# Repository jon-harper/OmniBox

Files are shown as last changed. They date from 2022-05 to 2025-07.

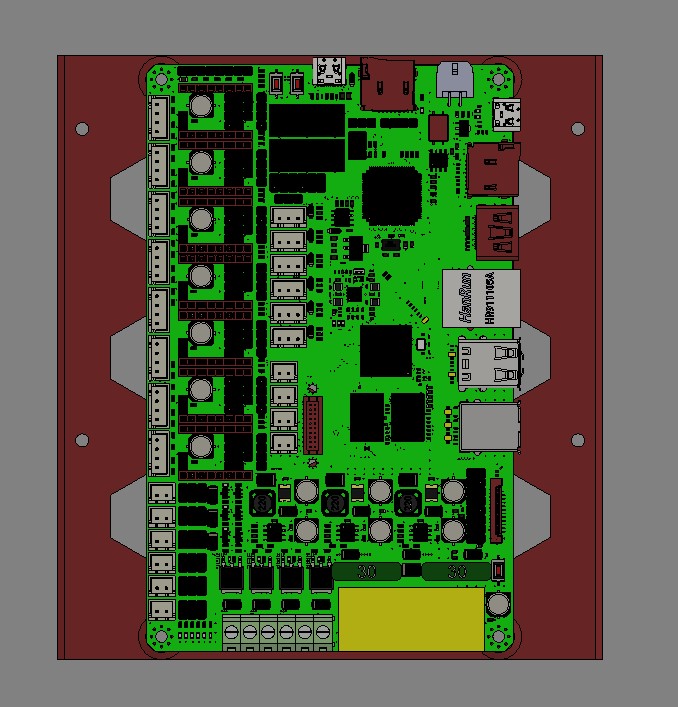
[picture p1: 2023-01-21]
Trays/MCU/MKS Skipr/Contrib/Screenshot 2022-11-25 044527.jpg

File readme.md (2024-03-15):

Welcome to the OmniBox repository! OmniBox is a modular, 3D printed electronics case for controlling 3D printers. It is conceptually derived from Steve Burcham's **[Stand Alone Main Control Case](https://github.com/bgdog1/3dPrinterCase)** V3.

This project focuses on modularity, accessibility to users, and reusability. The goal of OmniBox is to make your printer's electronics as valuable and re-usable an asset as the printer it controls.

## Documentation & Help

The **[Documentation][latest_docs]** includes a visual tour, a full bill of materials, list of supported parts, and guides for both printing and assembly.

Drop by the **[OmniBox Discord server](https://discord.gg/nKmJZMhfz5)** if you have other questions, or if you are simply curious!

## Current Release

v0.9.11 is the most recent stable version, released 2024/03/15.

- **[v0.9.11 Documentation][latest_docs]**
- **[v0.9.11 Changelog][changelog]**

photobooth picture

[changelog]: https://jon-harper.github.io/OmniBox/latest/history/
[latest_docs]: https://jon-harper.github.io/OmniBox/latest
[testing_changelog]: https://jon-harper.github.io/OmniBox/testing/history/
[testing_docs]: https://jon-harper.github.io/OmniBox/testing
[gallery_pic]:  https://jon-harper.github.io/OmniBox/0.9.11/img/examples/0.9.11/banner.png
[unstable]: https://github.com/jon-harper/OmniBox/tree/unstable

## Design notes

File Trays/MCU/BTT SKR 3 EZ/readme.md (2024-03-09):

# Trays/MCU/BTT SKR

## Overview

This tray mounts a BIGTREETECH SKR 3 EZ board. It is *not* compatible with the regular SKR 3.

- Category: MCU Tray
- Product: BIGTREETECH SKR 3 EZ
- Added: 0.9.9

## STL Files

### `MCU Tray - BTT SKR 3 EZ - M3.stl`

- Supports: No
- Mounting Hardware: 4x M3 x 6mm machine screws

### `MCU Tray - BTT SKR 3 EZ - M4.stl`

Note: M4 files are for users of 0.9.8 and earlier and are deprecated.

- Supports: No
- Mounting Hardware: 4x M4 x 6mm machine screws

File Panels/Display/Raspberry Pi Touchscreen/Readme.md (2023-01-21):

# Display Panel for Raspberry 7" Touchscreen

This plate mounts official Raspberry [Pi Touch Display](https://www.raspberrypi.com/products/raspberry-pi-touch-display/) to the OmniBox.

As the display is quite big, it covers the screw holes on the front body, so I recommend
installing the display first on the front part, before attaching it to the base.

Connect all the wires to the display first, both SPI and power, before mounting it to the plate.

There are two versions available, one is flush with the main body face and one is slightly raised.
The only differences are in the aesthetics and the screw size required.

- Flush version requires four M3x8 screws to mount the display. Both parts are attached to the main body first.
- Raised version requires four M3x16 screws to mount the display. You need to attach the plate first to the main body and then attach the display with the case to it.

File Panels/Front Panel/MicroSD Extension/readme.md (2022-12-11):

## Don't forget the SD Card extension files!

Make sure you also print the holder and cap files in `Misc/Micro SD Extension`.

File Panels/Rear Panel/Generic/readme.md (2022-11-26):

# Generic Panels

Each subfolder contains panels have cutouts to run wires through instead of panel mounts. Most users will want to use one of these.

There are still two configuration options:

## USB Port

- No USB panel mount
- USB B panel mount (SKR and most other boards)
- USB C panel mount (BTT Octopus and many newer boards)

Micro-USB to USB B panel mount connectors are available. Ex: Old Creality and many 8-bit boards use Micro-USB.

## 60mm Fan Cutout

Each panel has a version with this cutout if you want to use a 60mm fan instead of (or in addition to) the default dual 40mm fans.

These panels are all made from the same template. The source Fusion file also includes an 80mm fan profile if you'd like to go larger.

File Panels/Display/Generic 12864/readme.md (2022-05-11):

## Attribution

The contents of this folder are part of Steve Burcham's [3DPrinterCase](https://www.thingiverse.com/thing:3999751) project and are his designs. They have been slightly modified to remove some mounting holes.

## License

These files are individually licensed under the [Creative Commons - Attribution](https://creativecommons.org/licenses/by/4.0/) license.

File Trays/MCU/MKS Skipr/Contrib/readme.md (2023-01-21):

# MKS Skipr 1.0

This is a contributed tray for the MKS Skipr that uses 4mm long M3 inserts. These are more commonly found than the longer inserts used for the Core body.

## Credits

[Killajoedotcom](https://github.com/Killajoedotcom)

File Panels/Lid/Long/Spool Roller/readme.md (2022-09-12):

# Spool Roller Lid

The STL files in this folder are for a lid that doubles as a platform/mount for a spool roller.

This lid is based on my [Tighter T.U.S.H.](https://www.thingiverse.com/thing:4737072) filament roller project on Thingiverse.

This component was introduced in version 0.9.8.1.

## Bill of Materials

| Item | Qty |
|---|-----|
| `Lid - Spool Roller.stl` | 1 ea |
| `Spool Roller.stl` | 4 ea |
| M3 x 16mm machine screws | 4 ea |
| 608ZZ ball bearings | 4 ea |

## Instructions

1. Print one (1) of the lid file and four (4) of the spool roller files.
2. Set a spool roller flat in front of you.
3. There are two standoffs in on each side of the spool roller, both with holes in them. Set a 608ZZ ball bearing on each one.
4. The standoffs should go halfway up the center of the ball bearings. Take another spool holder and place it face down so that the standoffs meet in the ball bearing.
5. Insert an M3 screw in the left hole (the larger one) and screw it tight.
6. Flip the assembly over and insert an M3 screw in the left (larger) hole and tighten.
7. Repeat steps 2-6 to make another spool roller.
8. Snap the rollers onto the lid guide and adjust the distance between the rollers for brand of filament.

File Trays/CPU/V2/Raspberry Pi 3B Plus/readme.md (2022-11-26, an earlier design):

# Trays/CPU/Raspberry Pi 3B Plus

## Overview

This tray mounts a single Raspberry Pi 3B+.

- Category: CPU Tray
- Product: Raspberry Pi 3B+
- Added: 0.9
- Updated: 0.9.9

## STL Files

### `CPU Tray - RPi 3B Plus.stl`

- Supports: Recommended
- Mounting Hardware: 4x M3 x 6mm machine screws

### `CPU Tray - RPi 3B Plus with SPI.stl`

- Supports: Recommended
- Mounting Hardware: 4x M3 x 6mm machine screws
- Additional Hardware: 
	- 1x Micro Fit 3 panel mount connector, 2 Row, 6 Position (for SPI port)

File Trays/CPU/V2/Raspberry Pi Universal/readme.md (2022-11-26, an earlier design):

# Trays/CPU/Raspberry Pi 4B

## Overview

This tray mounts a single Raspberry Pi 3B+ or 4B. It is also compatible with clones that mount using the Raspberry Pi mounting hole pattern.

- Category: CPU Tray
- Product: Raspberry Pi SoC Form Factor
- Added: 0.9.9

## STL Files

### `CPU Tray - RPi with Fan.stl`

- Supports: Optional/use support blockers
- Mounting Hardware: 4x M3 x 6mm machine screws
- Additional hardware:
    - 1x 40mm fan
    - 4x M3 x 16 screws
	
### `CPU Tray - RPi with Fan and SPI.stl`

- Supports: Optional/use support blockers
- Mounting Hardware: 4x M3 x 6mm machine screws
- Additional hardware:
    - 1x 40mm fan
    - 4x M3 x 16 screws
	- 1x Micro Fit 3 panel mount connector, 2 Row, 6 Position (for SPI port)

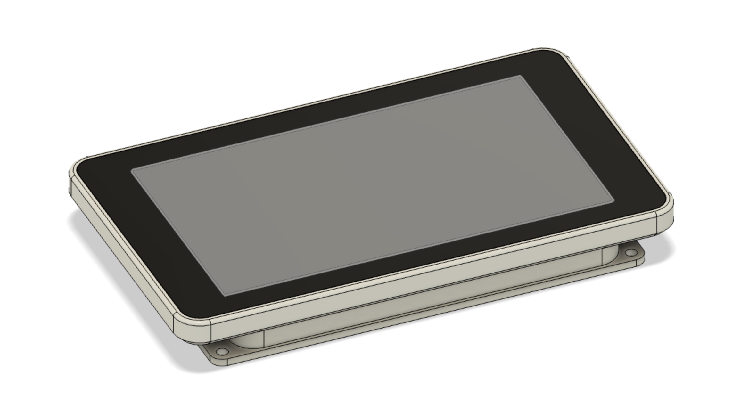
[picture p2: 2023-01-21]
Panels/Display/Raspberry Pi Touchscreen/raised/view_top.png

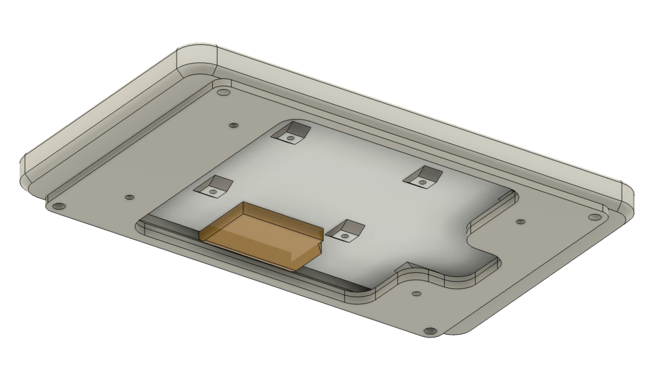
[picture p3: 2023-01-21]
Panels/Display/Raspberry Pi Touchscreen/flat/view_bottom.png

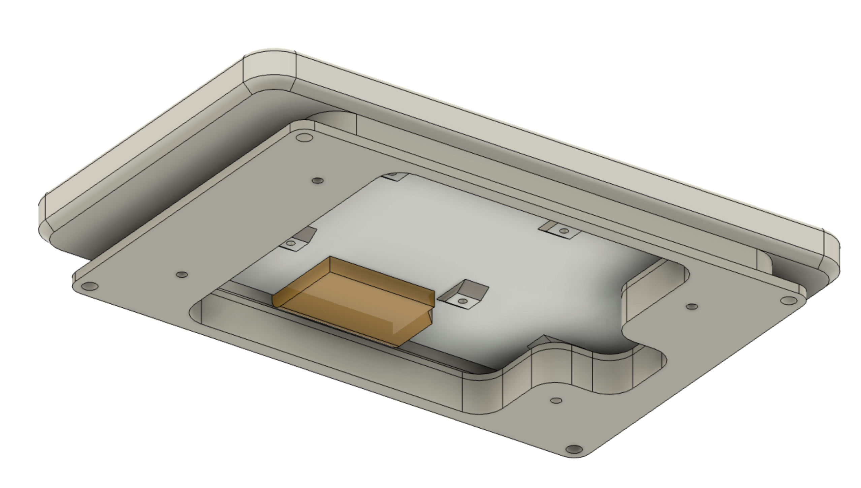
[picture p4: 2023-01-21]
Panels/Display/Raspberry Pi Touchscreen/raised/view_bottom.png

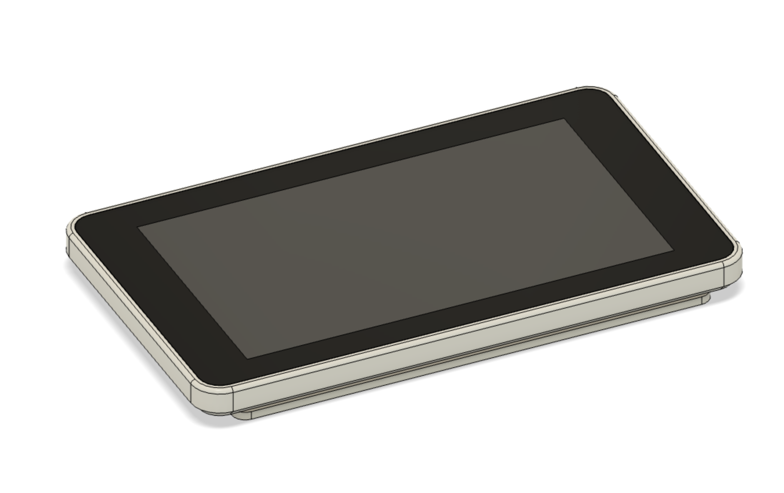
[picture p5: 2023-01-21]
Panels/Display/Raspberry Pi Touchscreen/flat/view_top.png

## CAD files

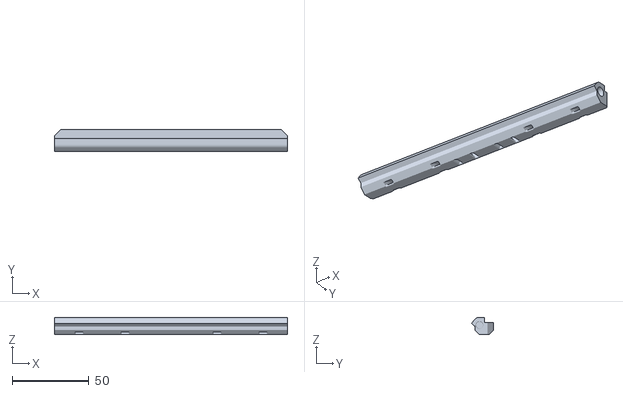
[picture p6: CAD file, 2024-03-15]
Core/Main Body/Crossbar/Main Body - Crossbar - HSI.stl
152.0 x 14.5 x 11.2

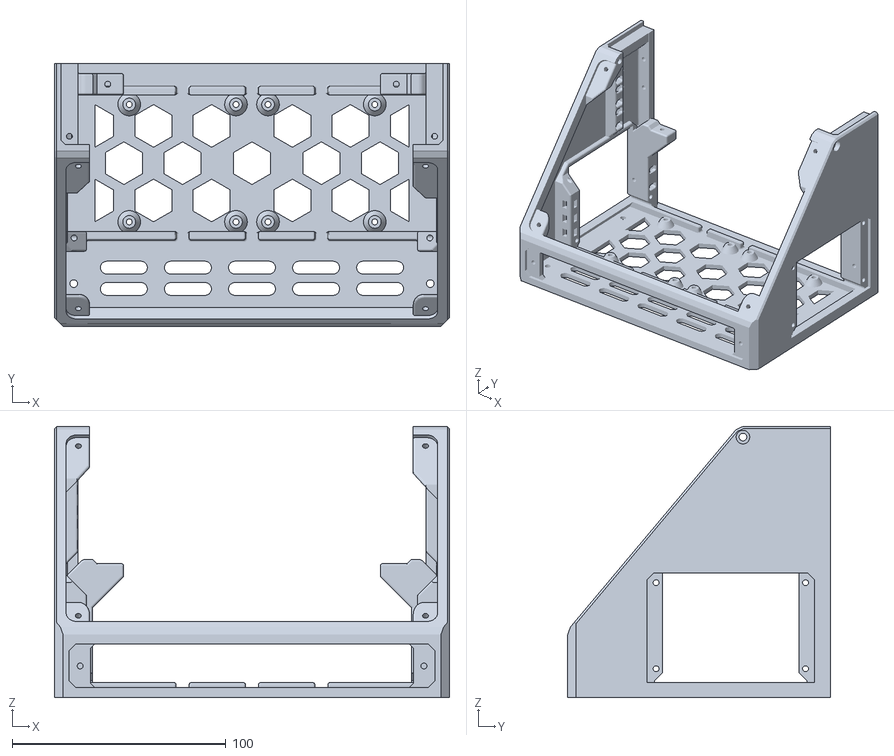
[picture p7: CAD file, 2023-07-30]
Core/Main Body/Front/Main Body - Front - Stock.stl
185.0 x 123.0 x 127.0

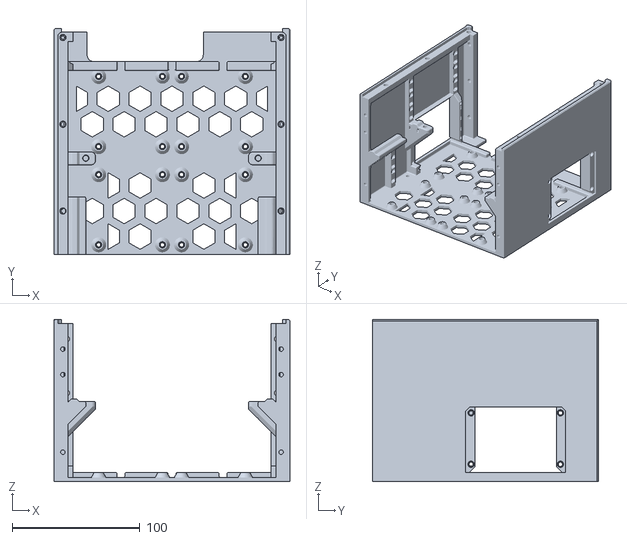
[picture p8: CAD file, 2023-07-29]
Core/Main Body/Rear/Main Body - Rear - Full HSI.stl
185.0 x 177.0 x 127.0

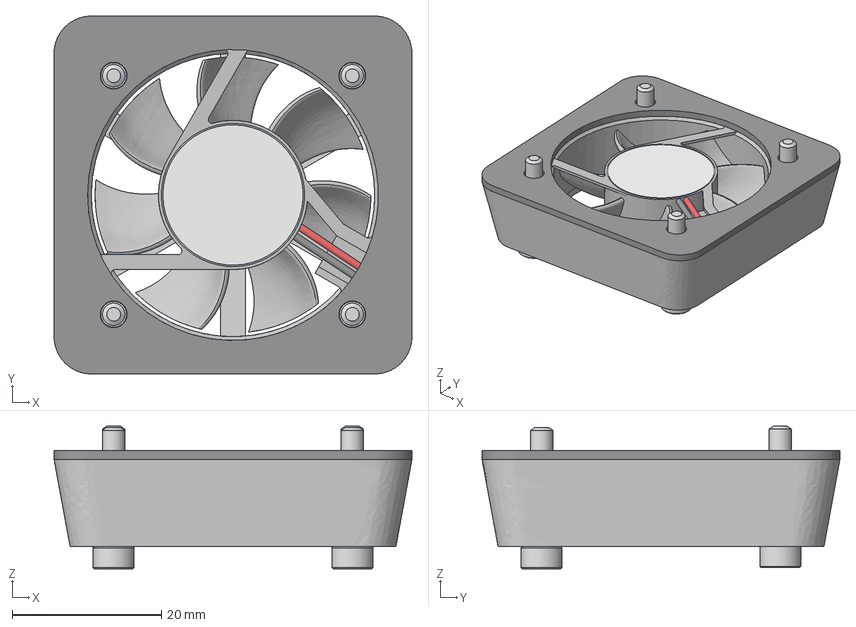
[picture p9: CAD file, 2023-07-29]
Fans/40x10/4010 Fan Assembly.step
48.0 x 48.0 x 19.2 mm
4010 Fan Cage
4010 Fan Gasket
PN503 x 4
PN700

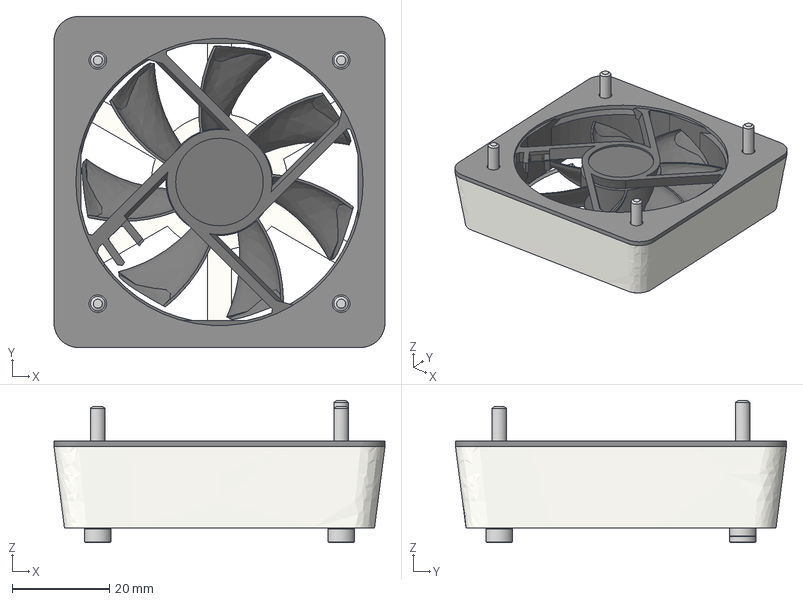
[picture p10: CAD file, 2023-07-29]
Fans/60x15/6015 Fan Assembly.step
68.0 x 68.0 x 29.2 mm
6015 Fan Cage
6015 Fan Gasket
PN505 x 4
Fan Wheel
Fan-Sunont_60x60x15mm

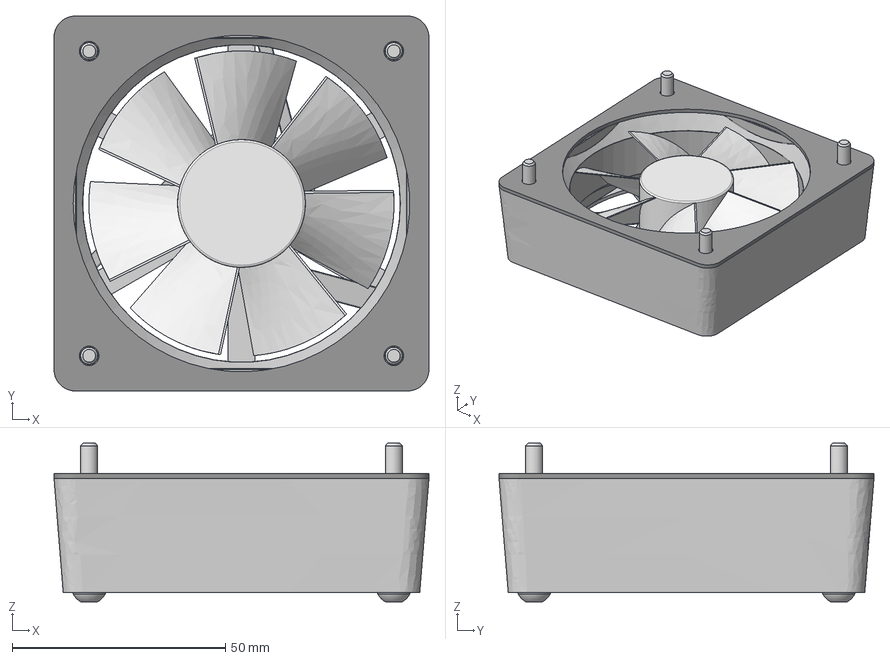
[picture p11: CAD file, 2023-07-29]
Fans/80x25/8025 Fan Assembly.step
88.0 x 88.0 x 37.2 mm
8025 Fan Cage
8025 TPU Gasket
80MM_FAN_PROP
80MM_FAN_HOUSING
PN517 x 4

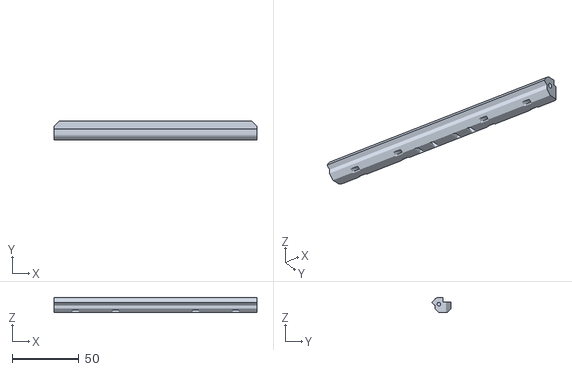
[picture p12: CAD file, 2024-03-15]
Core/Main Body/Crossbar/Main Body - Crossbar - Stock.stl
152.0 x 14.5 x 11.2

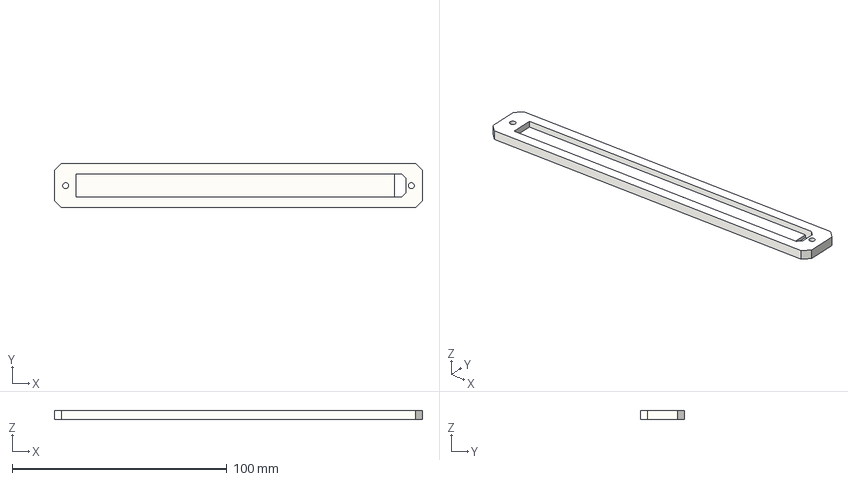
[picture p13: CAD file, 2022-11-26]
Misc/Front Panel LED Backer/Front Panel LED Backer - Full Length.step
171.4 x 20.4 x 4.20 mm

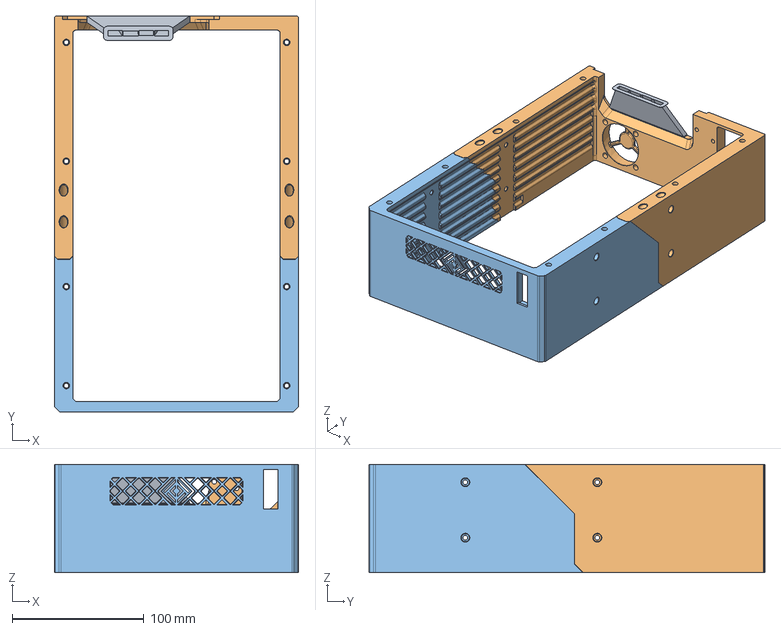
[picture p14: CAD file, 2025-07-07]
CAD/Double Base V4 - HSI.step
185.0 x 300.0 x 82.0 mm
Base Supports v4
Base - 70mm Front - HSI

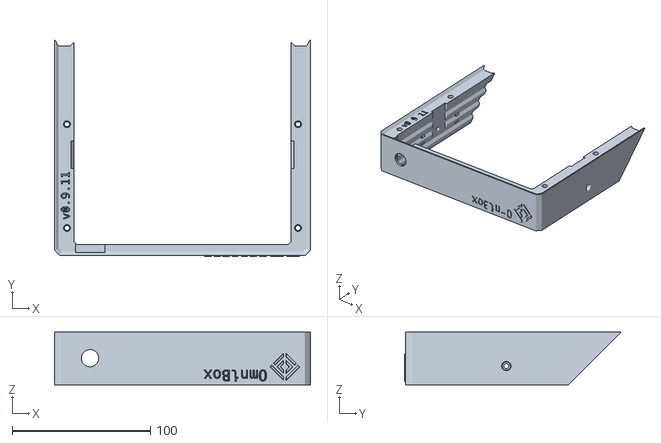
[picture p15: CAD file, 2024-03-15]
Core/Base/36mm HSI/Front/Base - 36mm Front - HSI with Toggle.stl
185.0 x 156.5 x 38.0

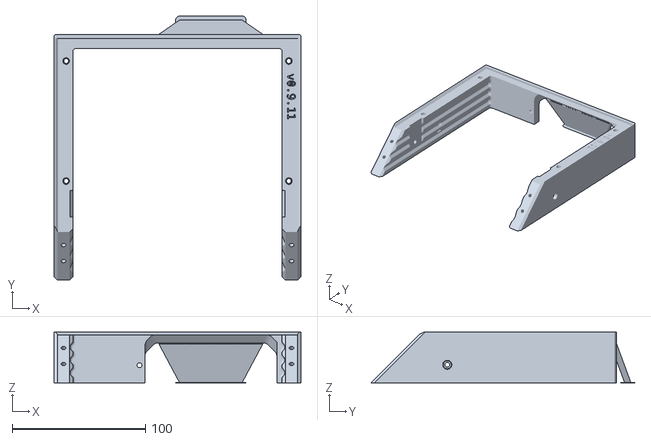
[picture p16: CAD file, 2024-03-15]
Core/Base/36mm HSI/Rear/Base - 36mm Rear - Basic HSI.stl
185.0 x 197.9 x 38.0

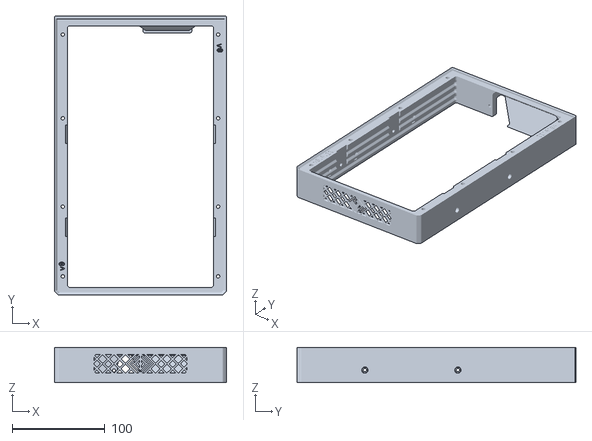
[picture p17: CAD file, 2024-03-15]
Core/Base/36mm HSI/Unified/Base - 36mm Unified - Basic HSI.stl
185.0 x 300.0 x 38.0

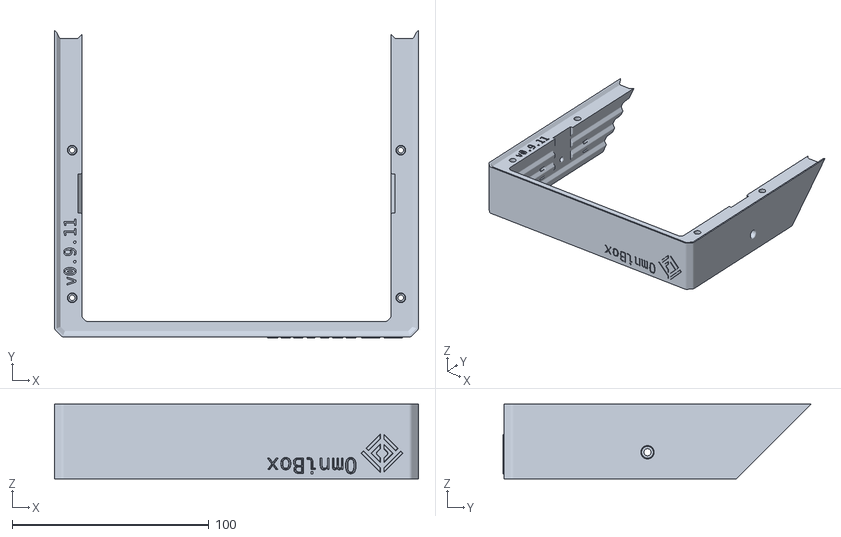
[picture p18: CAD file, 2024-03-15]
Core/Base/36mm Stock/Front/Base - 36mm Front - Basic Stock.stl
185.0 x 156.5 x 38.0

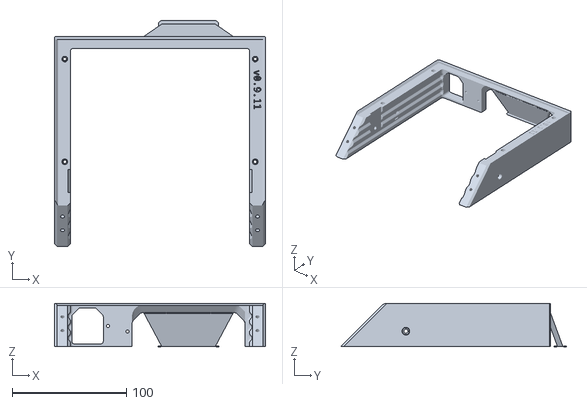
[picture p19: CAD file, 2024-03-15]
Core/Base/36mm Stock/Rear/Base - 36mm Rear - IEC Stock.stl
185.0 x 197.9 x 38.0

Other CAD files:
Core/Main Body/Front/Main Body - Front - HSI.stl
Core/Main Body/Front/Main Body - Front - Full HSI.stl
Core/Base/36mm Stock/Unified/Base - 36mm Unified - Basic Stock.stl
Core/Base/42mm HSI/Front/Base - 42mm Front - HSI with Rocker.stl
Core/Base/36mm HSI/Front/Base - 36mm Front - Basic HSI.stl
Core/Base/36mm HSI/Front/Base - 36mm Front - HSI with Rocker.stl
Core/Base/36mm HSI/Rear/Base - 36mm Rear - IEC HSI.stl
Core/Base/36mm Stock/Front/Base - 36mm Front - Stock with Rocker.stl
Core/Base/36mm Stock/Front/Base - 36mm Front - Stock with Toggle.stl
Core/Base/36mm Stock/Rear/Base - 36mm Rear - Basic Stock.stl
Core/Base/36mm Stock/Unified/Base - 36mm Unified - IEC Stock with Rocker.stl
Core/Base/36mm Stock/Unified/Base - 36mm Unified - IEC Stock with Toggle.stl
Core/Base/36mm Stock/Unified/Base - 36mm Unified - IEC Stock.stl
Core/Base/42mm HSI/Front/Base - 42mm Front - Basic HSI.stl
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

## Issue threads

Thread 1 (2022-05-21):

Lid screw holes are not symmetrical

jon-harper, 2022-05-21:
This is not a showstopper, but it does mean that the lid can only be correctly mounted one way and is not reversible.

I'm holding off fixing this until I hear feedback about using M3 screws for the lid versus using M4 (and possibly switching to M3 for the rear panel).

Closed 2022-07-02.

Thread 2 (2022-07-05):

SKR 1.4/2 profile is incorrect

jon-harper, 2022-07-05:
Screw holes for the SKR profile are the width of the board (~84mm), not the distance between the screw holes (~76mm).

This fix will be added to a hotfix release.

Closed 2022-07-07.

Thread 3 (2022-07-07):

BIGTREETECH PITFT support?

Majawat, 2022-07-07:
Love this project!

Any way you could add support for the BIGTREETECH PITFT screens? Either the 4.3", 5", or 7" (but 5" or 7" preferred).

https://www.biqu.equipment/collections/lcd/products/bigtreetech-pi-tft43-v2-0-screen-board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.

Not sure if you'd keep the PI mounted to the screen, or keep it in the tray (probably tray? though that'd require a longer DSI cable, which should be fine.)

jon-harper, 2022-07-07:
Steve's original project has a set of 5" files that are easily adaptable and set the TFT on the lid above the display. I don't have access to a PITFT myself, but if you're willing to fit test, I'm willing to make the adjustments for you.

I'll also take a look at the 7" and see what I can do with that. Bear in mind the case is 7" wide, so it may look slightly awkward.

jon-harper, 2022-07-11:
I've got CAD files for the display and Steve's mounts as reference. It looks like both the 5" and 7" will mount fine. The longer DSI cable is going to be necessary, btw.

I should have something for you to test before end of week. Which display are you getting, or do you have one already?

jon-harper, 2022-07-11:
Do what's best for you, dude. If you want the 7", someone else will come along to test the 5". 🙂

Majawat, 2022-07-11:
Haha, I definitely get what you're saying, just a hard decision for me. Ok, I'm going to go with the 5".

jon-harper, 2022-07-19:
Heya, Majawat. Hope you're well. I'm almost done with some bugfixes and such to get 0.9.7 out the door. Getting your Pi TFT going is next on my design list.

The simplest approach is to attach a hollow pillar to the Raspberry Pi screw holes in the back of the TFT. The ribbon cable can run through a hole into the center. I'm planning to make this pillar part of a half-length case lid that will sit up front.

I want to ask a few questions before I get too far, though.

1. What mounting hardware does the TFT come with? The [Amazon page](https://www.amazon.com/BIGTREETECH-Direct-Capacitive-Octoprint-Raspberry/dp/B08F1WMQ1J) shows brass standoffs and mentions M2.5 screws but doesn't list what hardware comes it ships with.
2. Will the screen look okay without an outer protective panel?

Thanks!

Majawat, 2022-07-19:
Lovely! I got the 5" last week and attached it just to get KlipperScreen working to play with.

1. No other hardware. Just the standoffs, screws, screen, and short cable.
2. I think so! There's a small bezel around the screen otherwise no features.
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
(Forgive the mess)

There is a small potential clearance issue with the display cable on the left. Or the brightness dial on the top right.

Let me know if you need any other info

jon-harper, 2022-07-19:
Thanks a ton for the pics! Unexpected and super helpful!

Can you tell me how long those standoffs and screws are? I'm probably going to hijack them to help mount the screen, rather than using the outer screw holes.

Majawat, 2022-07-19:
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

jon-harper, 2022-07-23:
[PiTFT Test 1.zip](https://github.com/jon-harper/OmniBox/files/9173872/PiTFT.Test.1.zip)

This is a test for fit file. If it works, the rest of the mount should work and I'll send you a full STL for the lid/stand combo.

Steps:

- Add the standoffs to the TFT in the Raspberry Pi holes;
- The standoffs should fall in to the holes in the tray;
- You should be able to use the stock 2.5mm screws to then tighten it.

If anything doesn't go as planned, lemme know! I guessed at the size of the holes for the standoffs. Right now they're 6.5mm, which should be loose enough. If they could be tighter or don't fit at all, likewise let me know.

Thanks again for testing this!

Majawat, 2022-07-23:
Seems pretty perfect.

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

I looked at the standoff holes, they're slightly big, but it's stable without needing to be tighter.

jon-harper, 2022-07-23:
[Lid - PITFT.zip](https://github.com/jon-harper/OmniBox/files/9174036/Lid.-.PITFT.zip)

Awesome! Here's the TFT mount, then. This is a half lid so that you can customize the back half still. I haven't uploaded that template yet but will soon.

I hope I got the slot for the flat ribbon cable in the right orientation.

Majawat, 2022-07-23:
I think I'm a bit confused. Where is this supposed to go on the box? Up top like this?

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

I was thinking it would have gone in the front, like here instead:
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

Majawat, 2022-07-23:
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
Also, it would probably be better if the cable came in through the side instead of the top if possible.

jon-harper, 2022-07-24:
> I think I'm a bit confused. Where is this supposed to go on the box? Up top like this?

Yes indeed. This is the format for the Pi TFT that Steve's case uses, and I admit I took the placement from him. The normal printer display goes below so that they appear stacked at an angle with the Pi TFT above.

Quick render:

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

> I was thinking it would have gone in the front, like here instead:

The 12864 or other LCD screen usually goes there. Are you planning to do entirely without? I can adapt the Pi TFT stand for the front easily enough, though I do still need to get the top version finished.

> Also, it would probably be better if the cable came in through the side instead of the top if possible.

Gotcha. I'll add a side cutout for the wire. Do you ever use the top cable port or any wiring on the other sides? Any issues with cable reach?

---

0.9.7 is almost packed up for release. When it's done today I'm going to create the 0.9.8 branch to add this and the MOSFET mount.

FYI, I also have a half-size lid to add that will go behind the Pi TFT screen and cover the back half of your case (with a handle, too).

Majawat, 2022-07-24:
> The 12864 or other LCD screen usually goes there. Are you planning to do entirely without?

Yep! I'm running Klipper on my RPI for an Ender 5 Plus. None of which supports the original screen without heavy software modifications (a different Klipper fork). So I'll only be using the PITFT.

I see no issues with the top print, so I'd call that one good!

(Sorry for the close/reopening, my finger slipped as I typed)

jon-harper, 2022-07-24:
Awesome! I'll go ahead and commit the Pi TFT lid, but I'll leave this issue open. It shouldn't take too much time to attach the modify a display template now that the fit work is done. I'll plan to have that to you (sometime =) this week.

jon-harper, 2022-07-26:
Howdy Majawat. Hopefully this works and is what you were looking for.

Closed 2022-08-18.

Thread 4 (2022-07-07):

Organizing MCU and Lower Bay Trays; Feedback Welcome

jon-harper, 2022-07-07:
The trays are multiplying.

Many of the MCU trays support multiple boards (the SKR and SKR E3, specifically).

I have two working profiles for LM2596 buck converters in the `Trays\Lower Bay` folder. I have a third to add yet. MOSFETs and SSRs can be added, but will have to be by request or submission as I don't have any on hand.

Note: I want to avoid cross-pollinating brands/types of bucks on the dual-buck trays, as there's no way I can manage that many combinations.

## Current Working Solution

This data should go in a Markdown README in each folder:

- Product name
- Image link
- Some kind of product page link

Links, in order of preference:

- A git repository
- A company's product page
- An Amazon or AliExpress link

jon-harper, 2022-07-23:
I have most of these done in preparation for 0.9.7.

jon-harper, 2022-08-17:
This issue is taken care of, although other folders need more attention for 0.9.9.

Closed 2022-08-17.

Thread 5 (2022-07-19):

Display mount screw profiles are off

jon-harper, 2022-07-19:
Currently the display mounting holes are approximately 0.5mm too narrow on each side, so only two screws can be used to mount a screen at a time.

This issue only impacts the front main body.

I expect to have this issue resolved by 7/20.

jon-harper, 2022-07-22:
The fixed version of this is available in the 0.9.7 branch. It affects *only* the `Main Body - Front.stl` file.

I am currently printing the parts for a final fit test before releasing 0.9.7 and merging with main.

jon-harper, 2022-07-23:
Bad news/good news:

- The display mount holes are off just slightly still, so only three of four screws will fit.
- This is better than two, and enough to hold the screen in place for this release.

Addendum:

The fundamental issue here is that the display panel is printed at a 40 degree angle. Because it's not vertical or horizontal, printing introduces a slight shift in the holes that I have to account for.

I have purchased some extra filament and found a way to get a test done in about 8.5 hours at a go. This will take time, however, and must wait for 0.9.8.

jon-harper, 2022-07-24:
I closed this early, but it *is* fixed.

Closed 2022-07-24.

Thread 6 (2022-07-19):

Ender 5 Plus MOSFET tray

Majawat, 2022-07-19:
The Ender 5 Plus has a bed heater MOSFET that I'd like to mount inside the OmniBox of course.

It seems to be a Creality specific part. But fortunately someone on Printables created a mount that includes the Octopus which might help getting the mount hole pattern: https://www.printables.com/model/171559-ender-5-plus-btt-octopus-mosfet-mounting-adapter

jon-harper, 2022-07-20:
[Lower Bay Tray - Creality MOSFET v1.zip](https://github.com/jon-harper/OmniBox/files/9147604/Lower.Bay.Tray.-.Creality.MOSFET.v1.zip)

Your link included a Fusion file. 👍

Let me know if the clearance is sufficient and the mounting holes deep enough. Or any other issues, of course. 🙂

Majawat, 2022-07-26:
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

Looks good to me

jon-harper, 2022-07-26:
Awesome! ✔

Closed 2022-07-26.

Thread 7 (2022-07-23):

TPU gaskets should cover more area

jon-harper, 2022-07-23:
The TPU gaskets currently only cover outside surface of the fan cage. They should also cover the fan except for the intake/exhaust hole. As is they are only minimally useful.

jon-harper, 2022-07-24:
Fixed in 0.9.7.

Closed 2022-07-24.

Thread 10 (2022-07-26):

Allow for more, smaller buck mounts and trays

jon-harper, 2022-07-26:
Referencing my [line of thought](https://twitter.com/jonspaceharper/status/1551865914349559809) on Twitter:

>First idea: Half-sized lower bay trays, to allow mounting up to four, smaller trays.
>- You could still simply use two large trays and keep the extra room.
>- This only requires adding 2 or 4 screw hole pillars that are otherwise unused.

Where right now the lower bay trays look like this:

```
[----------]   [----------]
|o        o|   |o        o|
|          |   |          |
|          |   |          |
|          |   |          |
|          |   |          |
|          |   |          |
|          |   |          |
|          |   |          |
|o        o|   |o        o|
[----------]   [----------]
```

Adding a few mounting standoffs would allow for more, smaller trays:

```
[----------]   [----------]
|o        o|   |o        o|
|          |   |          |
|o        o|   |o        o|
[----------]   [----------]

[----------]   [----------]
|o        o|   |o        o|
|          |   |          |
|o        o|   |o        o|
[----------]   [----------]
```

Which will let you still use the long trays, too!

```
[----------]   [----------]
|o        o|   |o        o|
|          |   |          |
|o        o|   |          |
[----------]   |          |
               |          |
[----------]   |          |
|o        o|   |          |
|          |   |          |
|o        o|   |o        o|
[----------]   [----------]
```

This will only affect the rear main body; there is no particular implementation timeline yet except pre-1.0.

jon-harper, 2022-08-03:
- Tested both sizes of new template.
- Mount generator template implemented
- Old bay trays are updated as needed

Closed 2022-08-03.

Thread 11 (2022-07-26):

Mean Well RSP-500-24 support

Majawat, 2022-07-26:
The mounting holes for the Mean Well RSP-500-24 do not match the current Core files. It is larger than the current files, taking up majority of the lower base.

Bonus if there was a way to add an extra fan to the case to fool down this large PSU.

jon-harper, 2022-07-26:
> The mounting holes for the Mean Well RSP-500-24 do not match the current Core files. It is larger than the current files, taking up majority of the lower base.

Oof, my bad for not considering this. I even have an SE-450-24 on a printer and knew the mounting holes are not universal.

I'll get a CAD file and get to work on this.

> Bonus if there was a way to add an extra fan to the case to fool down this large PSU.

Couple of thoughts:

- The new generic rear panels have 60mm exhaust fan that might help.
- I will look at a 40mm mounted low on the rear panel (next to the power connector), as well.
- Alternatively, a big ol' 92mm mounted midway up the rear panel would solve all of your problems.
- As for intake, I can make the "teeth" along the bottom of the base taller. That should increase airflow, too.

jon-harper, 2022-07-27:
Couldn't find a CAD, but the spec sheet works as well. The fourth screw hole is a bit odd--the RSP-500 has an "extra" M4 screw hole in the middle. You'll be using that instead of the corner screw  hole near the Raspberry Pi (it would require a tray redesign). Here's what I mean:

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

As always, let me know if you run into any issues.

---

P.S. I haven't modified the base yet to increase the intake "teeth" size. I'm pondering the idea of a universal PSU mount, so I'm hesitant to do too much right now.

Closed 2022-08-18.

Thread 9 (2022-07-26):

Allow replacing the MCU tray without removing rear panel

jon-harper, 2022-07-26:
Referencing my [line of thought](https://twitter.com/jonspaceharper/status/1551865917235232768) on Twitter:
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

This enhancement is targeted any time pre-1.0, i.e. when time allows.

This will only impact the rear main body and board trays and is backwards compatible—as all updates to Core should remain in the future.

jon-harper, 2022-07-31:
Confirmed fixed for 0.9.8.

Closed 2022-07-31.

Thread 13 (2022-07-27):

Power supplies require M4x6mm screws NOT 8mm!

jon-harper, 2022-07-27:
Opening this as an issue so I will not forget again.

Documentation needs to be amended as follows:

## /docs/bom.md

```
[-]M4 x 8mm, 14ea
[+]M4 x 8mm, 10ea
[+]M4 x 6mm, 4ea
```

## /docs/assembly.md / 2. Main Body

```
[-]- 4x M4 x 8mm screws (see caution below)
[+]- 4x M4 x 6mm screws (see caution below)

[...]

[-]    Do not use screws longer than 8mm to attach the power supply. Longer screws may touch components in the power supply and short or damage them.
[+]    Do not use screws longer than 6mm to attach the power supply. Longer screws may touch components in the power supply and short or damage them.
```

Closed 2022-07-27.

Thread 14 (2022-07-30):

Create universal PSU mount

jon-harper, 2022-07-30:
Related issue: #11

Adding in support for multiple power supplies is straightforward, but greatly complicates the export process. Additionally, the PSU is the only component that attaches directly to the case, rather than through a mount.

## PSU Specs

I looked up the most common Mean Well power supplies. The sides of their power supplies all mount at least two M4 screws on each side, evenly spaced from the midpoint (sometimes they are paired for four a side).

- Only one of the units that I looked at (all sub-500W) was too tall to fit within the 40mm tall base.
- Width and depth are not a problem.
- The screw spacing varies from 150-170mm between models.

## Solution

I have a fairly simple solution in mind that would let the PSU slide into guides in the sides of the base pieces. They can be secured with M4 screws that would pass through the base walls.

With a few mm of space between the PSU and main body "floor", I could then add a number of vent holes and let air run above the power supply instead of below. The vents would add rigidity to the base, reduce weight, and possibly reduce print time.

**I'm targeting the release after 0.9.8 to implement this.**

jon-harper, 2022-10-02:
I think I've finally come up with something for a universal PSU mount. Closing this will be the main determinant in the release of 0.9.9.

jon-harper, 2022-11-03:
Holding off closing this until I have an RSP-500 tray.

jon-harper, 2022-11-26:
I adjusted the qualification for closing this, since there is not a template available yet.

jon-harper, 2023-07-09:
A template exists but is not ready for release. Future changes mean this is remaining open for now, as well.

jon-harper, 2023-10-13:
Related: issue #118

jon-harper, 2024-03-05:
Template pushed! Closing!

Closed 2024-03-05.

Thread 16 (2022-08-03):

Newcomer documentation improvements

jon-harper, 2022-08-03:
Several things can be done to improve the experience for newcomers to the OmniBox website.

1. Add a few, small pictures near the top of the landing page to help with reader visualization. The only current pic is at the bottom and a render.
2. Add a version history/release log page for an at-a-glance update.
3. Explain stability guarantees between versions.

jon-harper, 2022-08-05:
Oops. Didn't auto-close.

Closed 2022-08-05.

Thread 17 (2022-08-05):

Pan and button head M3s will not work for the crossbar

jon-harper, 2022-08-05:
Button head and pan head screws do not work with the crossbar. The bored out hole is too small.

jon-harper, 2022-08-06:
I'm printing a 6.4mm wide hole now. That's two layers and should hopefully give plenty of clearance. I have button head screws here and will test.

jon-harper, 2022-08-07:
Fixed in 0.9.8.

Closed 2022-08-07.

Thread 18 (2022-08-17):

New front main body fan mount blocks screw hole for base

jon-harper, 2022-08-17:
The fan mount in the main body front intake partially obscures the M3/#6 screw hole underneath it for mounting the base. This is *not* a critical bug, and will be fixed in 0.9.9.

For now, inserting the screw at an angle or leaving it out resolves the issue. 0.9.8 remains on schedule with this bug.

jon-harper, 2022-10-02:
This was fixed while refactoring the core files. On track to close this with 0.9.9.

jon-harper, 2022-11-03:
0.9.9 Core is stable and has this fix. Closing.

Closed 2022-11-03.

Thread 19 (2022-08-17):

Add tray support for Solid State Relay

kameron-m7, 2022-08-17:
Feature Request: Add support for Fotek SSR-40 DA relay

[https://www.amazon.com/SSR-40DA-Solid-Output-24-380V-SSR-40/dp/B07FVHWN82](Amazon)
[https://grabcad.com/library/ssr-40-da-1](GrabCAD)
[https://cdn.sparkfun.com/datasheets/Components/General/SSR40DA.pdf](TechSpecs).

Thanks!

jon-harper, 2022-08-17:
Let me know how it fits and any suggestions you may have. I'm unsure if the slots that support the sides of the SSR are adequate to keep it from rocking.

jon-harper, 2022-08-17:
I revisited the dimensions and realized I *can* fit it on a half tray! The latest commit should do it.

kameron-m7, 2022-08-17:
Awesome, Thanks!

jon-harper, 2022-08-25:
Heya @kameron-m7, how does it fit? I want to make sure all is well before I close the issue. 😃

kameron-m7, 2022-08-26:
Fits well for me. Thanks!

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

jon-harper, 2022-08-26:
Awesome!

Closed 2022-08-26.

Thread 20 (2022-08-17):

Cram 2x Generic LM2596 onto half length tray

kameron-m7, 2022-08-17:
Is this possible? I am running out of space in my box. Thanks.

jon-harper, 2022-08-17:
You've got the two LM2596s, the SSR, and what else? I'll see what I can do, possibly adding a buck mount to the SSR tray.

kameron-m7, 2022-08-17:
Mosfet, and that's it for that part of the box.

jon-harper, 2022-08-17:
But the answer to your original question is yes, they will fit. 🙂

Closed 2022-08-17.

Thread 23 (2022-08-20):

Not all folders have readme.md files

jon-harper, 2022-08-20:
- The lids in particular are missing readme files.
- Individual display mounts also lack a readme with BOM.

jon-harper, 2022-11-26:
The documentation bypasses this. I'm instead trying to *remove* old readmes.

Closed 2022-11-26.

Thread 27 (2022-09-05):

Stackable Cases

jon-harper, 2022-09-05:
### Discussed in https://github.com/jon-harper/OmniBox/discussions/25

<div type='discussions-op-text'>

<sup>Originally posted by **jon-harper** August 25, 2022</sup>
Continuing a reddit discussion here!

> also, any thought on making them stackable?

I have thought about making them stackable, and was going to try and make such a lid until you came up with the idea of putting filament on top. I'm still definitely interested in the idea!

The holes in the base for attaching it to the main body pass straight through from top to bottom. This means 1) no supports needed but also 2) you can use the underside to mount things. Right now I just use the bottom for attaching [base extensions](https://jon-harper.github.io/OmniBox/assembly/core/#base-extensions), but they would be a good mounting point on the underside for some kind of interface with a lid.

I figure that the cases should just drop in place together, not fasten. Bottom case would have a lid that mates with the underside of the top case.

That's as far as I've gotten with it. 🙂</div>

------

Way overdue turning this into an issue. See most recent commits in 0.9.8.1 for latest. A slightly more refined version will be in the 0.9.8.1 release.

jon-harper, 2022-09-12:
:heavy_check_mark: Done.

Closed 2022-09-12.

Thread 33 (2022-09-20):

Base zip tie anchors need adjustment

jon-harper, 2022-09-20:
From [this discussion](https://github.com/jon-harper/OmniBox/discussions/32):

>Zip tie ports, great idea but that first one next to the power terminal has a really sharp bend at the spade connection that I am not a fan of. Perhaps move the rear circular cutout for the zipties 40mm to the front of the omnibox? Nitpicky but I probably wont use that ziptie port so the change is negligible.

Planning to get this cleaned up before 0.9.9 when the base gets universal PSU support.

jon-harper, 2022-10-02:
I've adjusted the most forward zip tie anchor slightly backwards and removed the rearmost anchors.

jon-harper, 2022-11-03:
0.9.9 Core is now stable; closing as fixed.

Closed 2022-11-03.

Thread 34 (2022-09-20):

Add intro section about larger/smaller screw holes throughout case

jon-harper, 2022-09-20:
Parts throughout the case use a larger/smaller screw hole pairing. Screw goes in larger hole then threads into smaller hole, using the smaller diameter to bind the threads. Since this is used throughout the case, a short intro paragraph will be helpful.

jon-harper, 2022-11-03:
Forgot to tag in commit. This is done.

Closed 2022-11-03.

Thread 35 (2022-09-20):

IEC socket hex nuts docmentation and improvements

jon-harper, 2022-09-20:
From [this discussion](https://github.com/jon-harper/OmniBox/discussions/32):

> When inserting the m3 nuts for the power terminal I would say that it really helps to use an m3x25mm to get the nut tightened into its recession by allowing you to poke the bolt through the hole and then snug the nut into place for the 16mms to go into after you remove the 25mm.

1. This will get added to the documenation.
2. I will look into improving that area of the case so that the "pocket" is more accessible.

jon-harper, 2022-10-07:
Update on this:

Fixed in the Fusion 360 model, but the base is still in progress with other changes.

jon-harper, 2022-11-03:
0.9.9 Core is stable, so closing this.

Closed 2022-11-03.

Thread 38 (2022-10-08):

Wago lever nuts?

jon-harper, 2022-10-08:
Mark Rehorst has a [Wago lever nut wire twister](https://drmrehorst.blogspot.com/2022/02/ultimate-3d-printed-wire-twister.html). That got me thinking of adding ways of using Wago lever nuts, particularly for splicing multiple fans together in the case.

- I figure that if a mount were added, 3-wire and 5-wire lever nuts will be the most commonly used.
- Lever nuts will probably also be used in pairs (+ and -).
- The simplest solution is to start with a lower bay tray.

I'm considering making mounting holes across from where the rear fans are. The lever nuts would fit in a holder that screws into the mounting holes. I'll start with the lower bay tray and gauge interest in built-in mounting holes after.

jon-harper, 2022-11-03:
Fit tested and ready to go in the 0.9.9 branch. I'm closing this in preparation for 0.9.9.

Closed 2022-11-03.

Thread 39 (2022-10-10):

Display screen partially blocks two front main body/base screws

jon-harper, 2022-10-10:
I had a less-than-perfect test print that curled slightly. Instead of being able to neatly thread in the #6 screws, I pretty much stripped one.

I've cut out a bit of the area behind the screen that the screws thread into. See below.

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

Fixed version of the front main body will be in 0.9.9.

jon-harper, 2022-11-03:
Core is now stable for 0.9.9, so closing this as fixed.

Closed 2022-11-03.

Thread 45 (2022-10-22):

Support for keystone jacks

jon-harper, 2022-10-22:
I have a working design for this, but haven't added it to any parts yet. It's a little late in 0.9.9, but I can at least export the shape or make a front panel with one or two sockets.

If it doesn't make it in 0.9.9, it'll definitely go in the next point release.

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

jon-harper, 2022-11-03:
I've committed a side panel and STEP template to 0.9.9, so support is added. I'd like to do a front panel as well before closing this issue, however.

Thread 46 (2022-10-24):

2 Request TFT 50 panel and BTT UPS 24V modual

wizard311, 2022-10-24:
I looked through the files and saw TFT35 style panels but nothing as large as TFT50.  Would also like a module for BTT UPS 24 to put inside the OmniBox.  Also is there a way to add 120MM fan to the omnibox?

jon-harper, 2022-10-24:
> I looked through the files and saw TFT35 style panels but nothing as large as TFT50.

I'll grab the CAD file and take a look at how to mount it.

> Would also like a module for BTT UPS 24 to put inside the OmniBox.

Definitely. I took a look at the dimensions and it may or may not fit on a short lower bay tray--I might need to use a long one.

> Also is there a way to add 120MM fan to the omnibox?

Yes and no. I used them early on since I had quite a few spare, though they would only fit on the lid. Also, you can get great cooling with even a [single 80mm in the back](https://github.com/jon-harper/OmniBox/tree/main/Panels/Rear%20Panel/Custom/Ender%205%20Plus).

At the same time, you're not the first person to ask about 120mm fans, so I'll see what I can do.

wizard311, 2022-10-25:
Thank you for the fast response.  I am converting a Elegoo Neptune 3.  Ok thats a lie the only thing left of the neptune is the frame as I have changed it over to Exoslide y and xz for movement and BTT S40C X and Y closed loop steppers, Dual Z steppers, Octopus Pro and Raspberry Pi 4. Also changed over to E3D Revo and Orbiter Extruder. The Neptune 3 just doesn't have a lot of room to mount things so your OmniBox is a blessing at this stage in my conversions. Thanks again for this perfect answer I didn't know I needed.

jon-harper, 2022-10-25:
I'm glad to help! That sounds like an awesome machine you've got, and might become the first resin printer on an OmniBox.

I can't promise timelines on getting parts to you, but are you comfortable if I upload zipped STL files to this issue for you to print and fit test? I don't have the two BTT parts here, just CAD models.

Finally, a compatibility question: are you using a Mean Well LRS-350 power supply or something else?

wizard311, 2022-10-25:
I am fine with zipped STL files.  I have LRS-350 at the moment but I am looking to upgrade to RSP-500-24.

jon-harper, 2022-10-25:
Cool, just making sure. ✔

The next OmniBox version (0.9.9) coming out next month will have universal support for power supplies, by the way (you'll be able to remove the PSU and replace with a different model).

jon-harper, 2022-10-25:
[BTT TFT50 Test Fit.zip](https://github.com/jon-harper/OmniBox/files/9860946/BTT.TFT50.Test.Fit.zip)

I got really lucky here. The project that OmniBox is based on had a file for this that I could adapt. BTT didn't release a CAD model for this display, so I can't even do a cursory check for fit myself.

It might take some fussing to get this right, but it should be close to start.

jon-harper, 2022-10-25:
Your timing is pretty spot on. I closed out the 0.9.9-experimental branch and folded it into 0.9.9 a few hours ago. Any changes from here to release for the Core body are likely to be cosmetic.

Please be aware that 0.9.9 is still an active branch, too. I'm still making sure all of the new and changed panels and trays are exported and merged, as well as testing a few. Use at your own risk, as it were. 🙂

jon-harper, 2022-11-23:
Hey, I'm checking on all of the open issues for product support. I'm hoping to release by week's end and want to include everything tested to fit that I can. If you've fit any of the trays or panels requests, can you let me know how it went?

Many thanks!

wizard311, 2022-11-24:
I am still attempting to print all the parts for the OmniBox. I know the
display panel BTT50 doesn't fit in is current rendition.  I am not very
good with any type of CAD software so I inserted the panel in the front
part of the OmniBox and "deleted" the BTT50 from it to create the void
necessary to install the BTT50 in the real world.  I know this is backwards
from the way it's supposed to be done but again I am not talented in using
CAD software.

I haven't finished printing the other custom parts you have provided for
me.  My printer only prints at 30ms so these are taking days per print.
Once I have all of them printed I have another idea I want to run past you
but I have to get it assembled to test my idea.

Thanks again for all your hard work.

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

jon-harper, 2022-11-25:
Thanks for getting back to me. Just wanna make sure I have stuff in the right place before release. 🙂

I'll check on the BTT display. Sounds like I left the actual panel to attach it to the case. 🤦‍♂️

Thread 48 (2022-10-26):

[MCU Tray] - BTT SKR3 & BTT SKR 3 EZ

florence-wolfe, 2022-10-26:
## Request details

Both the recently released SKR 3 and SKR 3 EZ boards have different screw positions than the other SKR 1.3+ boards.

- In the case of the SKR 3, there's only a 0.2mm difference, since they seem to have added a bit of padding.
- In the case of the SKR 3 EZ, however, it's trickier and would require a new layout since the board shifts the top-right screw hole to accommodate one of its EZ sockets.

The [BTT SKR 3 Repo](https://github.com/bigtreetech/SKR-3) contains the sizing PDF as well as step files to make easier modifications and design new parts for the boards.

### Affected Components

- MCU Tray
- Documentation

jon-harper, 2022-10-26:
Thanks a ton for catching this.

I'll get something put together shortly. Are you willing to fit test if I attach the results here?

francis-robert, 2022-10-26:
Yeah, I would absolutely do that. I only have the SKR 3 EZ and not the 'standard' SKR 3 board though. Then again, it's arguably the more important of the two to test.

I also added an edit to the top post since I just realized the documentation would also need to be updated to reflect that the current designs aren't actually all SKR 1.3+ boards and there may be subtle variations between SKR variants

jon-harper, 2022-10-26:
I really appreciate it. I will get a tray for the SKR 3 EZ to you today.

jon-harper, 2022-10-26:
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
[BTT SKR 3 EZ.zip](https://github.com/jon-harper/OmniBox/files/9871965/BTT.SKR.3.EZ.zip)

Here it is. You likely want the M4 version (`MCU Tray - BTT SKR 3 EZ - M4.stl`) unless you're an early bird and are printing an 0.9.9 case.

jon-harper, 2024-11-28:
I'm going to close this as complete unless I hear otherwise. It's been years.

Closed 2024-11-28.

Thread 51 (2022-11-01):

Basic LM2596 mounting holes are incorrect

jon-harper, 2022-11-01:
I apparently failed to verify the mounting hole positions for basic LM2596 buck converters. I think they got messed up when switching to the auto-generated templates.

Regardless, the trays are incorrect. I will merge in a fixed to the main branch today.

Closed 2022-11-01.

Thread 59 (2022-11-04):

Micro Fit 3 pinouts for rear panels are missing

jon-harper, 2022-11-04:
I have a pin guide for using Micro Fit 3 connectors to help plan ahead when creating wiring harness. It's really handy if you use a rear panel with panel mount MF3 connectors (or if you just rewire your printer with them).

I doubt I'll fit this in before 0.9.9, but I'd like to include the file with the Molex Micro Fit 3 rear panels eventually.

jon-harper, 2023-01-21:
[The Clockmaker Project - Panel Mount & Wiring Harness Tips](https://jon-harper.github.io/clockmaker-project/wiring/panel_tips/)

Closed 2023-01-21.

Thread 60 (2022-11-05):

RSP-500 does not fit in the stock base

jon-harper, 2022-11-05:
I am working on a solution, but the RSP-500 does not fit in the base area of the case. This affects all versions, including 0.9.9.

jon-harper, 2022-11-05:
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

1. Either print the unified base or follow the regular version directions.
2. Then print the PSU tray to attach the power supply.
3. Note that if using an older case, you'll need to use M3 screws for the bottom two screws on the rear panel with this base.

## Unified Version

[Extended base, unified version](https://github.com/jon-harper/OmniBox/blob/051a580c46da5d54c024ee7dff6a594fa0ccc031/Core/Base/Unified/Base%20-%20Extended%20Unified.stl)

You will need to choose between stock and with heat sink inserts.

## Regular Version

- [Extended front STL](https://github.com/jon-harper/OmniBox/blob/0.9.9/Core/Base/Front/Base%20-%20Extended%20Front.stl)
- [Rear and rear extension STLs](https://github.com/jon-harper/OmniBox/tree/0.9.9/Core/Base/Rear): print the rear extension, then pick either stock or with heat sink inserts (HSI).

## PSU Tray

Print the PSU mounts for the RSP-500 [here](https://github.com/jon-harper/OmniBox/blob/69ff07e1fb1a74174a7a0fb8d2d8e737c4af098f/Trays/PSU/Mean%20Well%20RSP-500).

This is the base from 0.9.9 but will fit with the main body from older cases (back to 0.9.7, I believe).

## Discussion

This still requires fit testing and I am open to feedback.

jon-harper, 2022-11-05:
It looks as if the new PSU tray will be fine for the RSP-500. Users of 0.9.7/0.9.8 can replace the base to switch to the RSP-500 if needed. Closing as fixed.

Closed 2022-11-05.

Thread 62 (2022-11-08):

Panel mounted connectors template is out of date

jon-harper, 2022-11-08:
The Fusion 360 file for panel mounts is now incomplete and out of date.

It needs a pretty thorough overhaul, tbh.

- I've tested a Micro Fit 3 profile that's slightly wider and less awful if there's any elephant's foot present.
- Keystone jacks need to go in there, too.

jon-harper, 2023-03-16:
Fixed in [this commit](https://github.com/jon-harper/OmniBox/commit/06d76b338058d0acc5d394015d5e1ed77c7ca923).

Closed 2023-03-16.

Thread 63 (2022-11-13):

Request BIGTREETECH Relay V1.2 Bottom Plate

wizard311, 2022-11-13:
I am wanting to add a BTT Relay V1.2 to the Omnibox I used the file from this thingiverse as a blueprint and the bottom plate from "Lower Bay - DROK 5A Buck with LED" to start a file for it but I feel it could use supports for the screw posts and possibly wire ties like the "Lower Bay - DROK 5A Buck with LED".  I attempted to keep the mounting post at the same height to fall into your ecosystem.  Please feel free to make any and all changes to create this part for Omnibox ecosystem.

https://www.thingiverse.com/thing:4428092
[BIGTREETECH Relay V1.2.zip](https://github.com/jon-harper/OmniBox/files/9997702/BIGTREETECH.Relay.V1.2.zip)

jon-harper, 2022-11-14:
Cool! I'll see what I can put together. This will give me a break from documentation writing, too. 🙂

jon-harper, 2022-11-16:
[Here's the folder in the unstable branch](https://github.com/jon-harper/OmniBox/tree/0.9.9-unstable/Trays/Lower%20Bay/BTT%20Relay%201.2).

I put a pair of zip tie anchors on one side, then decided to make it symmetrical. They anchors are really close to the edges so that you have room for that rather long board. If I moved them too far out and it's inconvenient, I can adjust.

Let me know how it goes. 👍

wizard311, 2023-04-08:
Test fit complete and perfect fit and function

jon-harper, 2023-04-08:
Thanks for letting me know!

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

Closed 2023-04-08.

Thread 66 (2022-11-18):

Question about Beta/Unstable 0.9.9

wizard311, 2022-11-18:
I try to back up your 0.9.9 files as they change and I found that PSUs folder is now missing was there an issue with the Mean Well LRS-350 file?  Second question is there plans for a Mean Well RSP-500-24 file?  I have 2 of these headed my way to install on my 2 printers and really want to drop them in the Omnibox to get rid of the Mean Well LRS-350 I currently run.  I can not open step files but I have included the drawing file from Mean Well hoping it has the mounting points included to help with file creation.

Thanks for all you do

[RSP-500-3D.zip](https://github.com/jon-harper/OmniBox/files/10036932/RSP-500-3D.zip)

jon-harper, 2022-11-18:
My bad! I use GitHub for software projects so I'm really used to it. I need to do a better job accounting for that.

### What's Happening

First, let me kinda explain what I *think* is going on. GitHub is centered around file versions, and has "branches". I [wrote up short thread](https://twitter.com/TheOmniBox/status/1584092748029648898) about how git works and used OmniBox as an example. This may help explain things.

The pic below shows the OmniBox branches:

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

`0.9.9-unstable` has the stuff that's not fit-tested (like the RSP-500 file). Once it's tested, it goes into `0.9.9-beta`.

GitHub makes it really easy to accidentally switch back to the main branch, though. So you might be looking at `0.9.9-unstable` and accidentally wind back up in the `main` branch. Another user had a similar issue and accidentally printed the wrong base, so clarifying this is definitely something I need to address.

### Fixing It

There's two easy ways to fix this for you:

- Download a Zip copy of the 0.9.9-unstable
    - Has a straight copy of the files
    - Probably the simplest solution for now
- Use GitHub desktop
    - It's kinda like OneDrive or DropBox but for GitHub.
    - You can just browse the files on your hard drive.
    - Lets you set the branch you're working with, too.

Either way, go to the `0.9.9-unstable` branch and hit the green "Code" button and switch to the "Local" tab, like below. From there you can download the Zip or open the branch in GitHub Desktop.

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

Lastly, [here's a direct link to the RSP-500 folder in the unstable branch](https://github.com/jon-harper/OmniBox/tree/0.9.9-unstable/Trays/PSU/Mean%20Well%20RSP-500).

Closed 2022-11-18.

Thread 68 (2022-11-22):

Support for 12mm - 12.5mm power switches

jon-harper, 2022-11-22:
This would be nice. Requested by Level Fun Games via Twitter.

- Would require a new base version, but there is only one front base version ATM.
- Would also add more universal base versions...
- Maybe done as front panel option? Offer a version of the base without a switch?
- Gives the option of a reset button next to it (which won't fit in the base).

Targeting release after 0.9.9.

jon-harper, 2023-03-23:
I've added a version of this to `unstable`: https://github.com/jon-harper/OmniBox/commit/1496ec4ccc7531d10752d829810a0926ec6c3f15

I've done a fit test with a 12mm switch and have updated the 0.9.10 BOM. Closing for now.

Closed 2023-03-23.

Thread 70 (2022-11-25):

[MCU Tray] MKS Skipr

Killajoedotcom, 2022-11-25:
### UNTESTED. My submission for the MKS Skipr

Wanted to use a spare MKS Skipr motherboard but noticed only BTT stuff was supported. Generated this version for myself, but wanted to give back to the project because it's so good. I have yet to print and test this, but it uses M3 heatserts for longevity.

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
[MCU Tray - MKS Skipr - Heatserts.zip](https://github.com/jon-harper/OmniBox/files/10091813/MCU.Tray.-.MKS.Skipr.-.Heatserts.zip)

If good enough, I hope this can be added to the project eventually.

jon-harper, 2022-11-25:
Thanks!

I made a note on the PR that I totally messed it up. I've cherry-picked the files into `-unstable` and will fix up a version with stock screw holes, too.

Let me know how the fit test goes; once I've done my end and the fit test is okay I'll close this.

jon-harper, 2022-11-27:
Your tray looks great! I believe your design is for the 4mm long inserts? They're much more common than the ones I use in the rest of the case so I kept your design and added one for the 5.7mm long inserts and one without inserts at all (like standard trays).

Killajoedotcom, 2022-11-27:
>

Yes, I build Vorons quite frequently and have hundreds of the M3x5x4 heatserts on hand. Thanks for making other versions.

jon-harper, 2022-11-27:
> Yes, I build Vorons quite frequently and have hundreds of the M3x5x4 heatserts on hand.

This...is something I very much should consider moving forward.

> Thanks for making other versions.

Thanks for suggesting the board *and* making the first one!

jon-harper, 2023-01-21:
Got this in the docs now. Closing.

Closed 2023-01-21.

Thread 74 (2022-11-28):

MakerBase MKS Monster8 support

jon-harper, 2022-11-28:
This is a placeholder issue until a fit test is completed.

3D-Experiments, 2024-08-02:
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

Fits on carrier with heat set inserts installed. I will try fitting carrier board into case once I'm done printing the rest.

jon-harper, 2024-08-03:
Thanks!

Closed 2024-08-03.

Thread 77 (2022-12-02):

PSU switch should always be on load side

jon-harper, 2022-12-02:
> It’s a safety thing. A switch will work on the hot or the neutral, but if you switch the neutral, the light fixture is still electrically live even with the switch turned off.
>
> You really don’t want that. In the event of a ground fault or other problem at the light socket, you want to be able to kill power to it from the switch.

Quoted from somewhere else.

- Remove references to black wire in BOM
- Remove references to switching on neutral in assembly

jon-harper, 2022-12-03:
Okay, I pushed an updated documentation build for this.

Closed 2022-12-03.

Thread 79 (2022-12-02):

SKR board need to be turned sideways or use a longer SD extension

jon-harper, 2022-12-02:
Standard BOM SD card extension is too short. Testing was done with a longer extension.

Alternative is to rotate board. Will likely do this.

[Link to a longer MicroSD extension](https://www.amazon.com/gp/product/B07YYSP5F5).

jon-harper, 2022-12-10:
This also affects the SKR V3 & V3 EZ.

Rotating the board will become problematic with longer boards. It looks more like each board description will come with a "short or long" field for which length of MicroSD extension to get.

jon-harper, 2022-12-10:
1) The BOM and other entries now mention that a short or long extension is needed.
2) The MCU tray entries specify which one to use.
3) The assembly specifically calls this out, as well.

Closed 2022-12-10.

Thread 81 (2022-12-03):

Lower bay tray standoffs need a fillet

jon-harper, 2022-12-03:
The standoffs for the lower bay trays snap too easily. A 2mm fillet would fix this.

Also can punch out the bottom of the hole to save time and allow longer screws.

jon-harper, 2023-01-13:
Fixed with most recent `unstable` branch [commit](https://github.com/jon-harper/OmniBox/commit/fa1d6676cd8561b256c17cd0c2f12089033bdf4b).

Closed 2023-01-13.

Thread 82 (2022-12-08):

BOM SD extender not fitting?

phillyaws, 2022-12-08:
Hi!  Printed out the [SD Card extension](https://github.com/jon-harper/OmniBox/tree/main/Misc/Lanmu%20MicroSD%20Extension) for the front panel, and the [extender in the BOM ](https://smile.amazon.com/LANMU-Extension-MicroSDHC-Monoprice-Raspberry/dp/B07WWVBK8V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)doesn't seem to fit.  Is the BOM wrong, or am I?

jon-harper, 2022-12-08:
Are you using an SKR 1.4 or 2 by chance? Someone testing it found that problem about a week ago(issue #79 )

If it's another board...new bug!

In the mean time, [this has a longer extension](https://www.amazon.com/gp/product/B07YYSP5F5) as a workaround, with my apologies.

phillyaws, 2022-12-08:
Oh, I mean the physical card...holster?  Receptacle?  I'm not sure of the technical name, but the black plastic part of the extender is too big for the file mount.

jon-harper, 2022-12-08:
Ah. No worries. Pry it open and remove the PCB inside. :-)

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

jon-harper, 2022-12-10:
Hey, I'm just making sure that this fixed the problem for you before I close the issue.

I'm going to either figure a way to illustrate that step or make it a visible note. It's easy to miss since it's just a line of text without a graphic.

phillyaws, 2022-12-10:
> Hey, I'm just making sure that this fixed the problem for you before I close the issue.
>
> I'm going to either figure a way to illustrate that step or make it a visible note. It's easy to miss since it's just a line of text without a graphic.

I'm going to check when I get home today!

phillyaws, 2022-12-12:
It worked perfectly!  Now I just need to figure out how to use Fusion to make rear/sideplates, and I'm home and hosed!

jon-harper, 2022-12-12:
Awesome! Thanks for checking back, too!

It may not be what you need, but opening one of the existing design files
will demonstrate a working example that you can modify. Good luck!

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

Closed 2022-12-12.

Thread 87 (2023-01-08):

MCU Tray - Fysetc Spider

MaffooClock, 2023-01-08:
I've used the template to design a MCU tray for the [Fysetc Spider](https://wiki.fysetc.com/Spider/).

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

I've opened PR #86 for you to review and consider.

jon-harper, 2023-01-08:
Thanks! Have you had a chance to fit test yet?

MaffooClock, 2023-01-08:
I have not, but I am printing it at this very moment, and will share a photo of the MCU mounted and the tray inside the body.

jon-harper, 2023-01-08:
Rock on, thanks!

MaffooClock, 2023-01-08:
Wahoo, it works!  Even though I haven't finished assembling my OmniBox, I don't see any clearance or wiring issues at this point.

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

jon-harper, 2023-01-08:
Sweet! I'll get this merged and in the docs; leaving it open for now (so I don't forget). Thanks for the design!

jon-harper, 2023-01-21:
It's in the docs. Closing.

Closed 2023-01-21.

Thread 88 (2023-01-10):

BTT PI TFT43/TFT50

MaffooClock, 2023-01-10:
[The documentation](https://jon-harper.github.io/OmniBox/0.9.9/support/displays/#raspberry-pi-displays) lists the BTT TFT43/TFT50/TFT70 product family specifically, and I purchased a TFT50 so that I could have it in the front panel rather than on the lid.

I see you've added a display panel for the PI TFT50 in commit a3d2cb5, but I'm confused by [the design](https://github.com/jon-harper/OmniBox/blob/f1a972f000c8eb2b4fda452bd85436bae8aea70d/Panels/Display/BTT%205.0%20TFT/Display%20Mount.stl).  It appears to be similar to the smaller LCDs that include a knob, however, the PI TFT43/TFT50/TFT70 family are just capacitive touch displays (no knob).

I must be confused, and the [Panels/Display/BTT*](/jon-harper/OmniBox/tree/unstable/Panels/Display) files must be for a different product family.  Are the TFT43/TFT50/TFT70 files somewhere else and I'm just not smart enough to find them?

For reference, this was discussed in these issues:
  - #3
  - #46

Not complaining!  Figured I'd stumbled into some ambiguity between panel files and documentation that ought to go on the to-do list 🙃

As I mentioned, I have a [TFT50](https://a.co/fCm2DUI) coming (should be delivered today or tomorrow), and I'd be happy to help with fit-test or even designing a panel for it to contribute here.

By the way, thanks for sharing such a fantastic project, and for being so helpful and involved.  I am eager to contribute as much as I can.

jon-harper, 2023-01-10:
TL;DR: The [Raspberry Pi Display](https://github.com/jon-harper/OmniBox/tree/main/Panels/Display/Raspberry%20Pi%20TFT) is what you're looking for. It mounts using the Raspberry Pi screw holes on the back of the display, so any screen  meant for an RPi works with it.

---

Ah! There are two different products called TFT50 and you've *definitely* stumbled on some documentation ambiguity.

There's the ["BTT TFT50"](https://www.amazon.com/BIGTREETECH-Direct-Printer-Display-Screen/dp/B08B34CXTV), which is for MCU displays and is a touchscreen plus knob. Then there's the ["BTT PI TFT50"](https://www.amazon.com/BIGTREETECH-Screen-Display-800x480-Raspberry/dp/B08FD2YZ23), which is is *just* a touchscreen as is for the Raspberry Pi.

The confusion about which product it references is that:
- the plain TFT50 display isn't documented yet (an oversight)
- the docs don't link to the PI TFT50 files (ditto).
- The GitHub readme is also way out of date and mentions none of these (ditto refrain).

I've tagged this issue as a doc bug and am leaving it open until I've reworked that section of the documentation.

-----

> By the way, thanks for sharing such a fantastic project, and for being so helpful and involved. I am eager to contribute as much as I can.

Thanks! I really appreciate that. And thank you for contributing, including finding this issue; every hand helps.

MaffooClock, 2023-01-10:
> The [Raspberry Pi Display](https://github.com/jon-harper/OmniBox/tree/main/Panels/Display/Raspberry%20Pi%20TFT) is what you're looking for...

💡 Ah.  I saw that, but kept thinking it was specific to the [official Raspberry Pi Touch Display](https://www.raspberrypi.com/products/raspberry-pi-touch-display/) (which I understand would be a top-mount only; I was confusing myself).  Further, I was a bit thrown off by how it's just a flat panel with vent holes, so I never gave it any further thought.

> ... It mounts using the Raspberry Pi screw holes on the back of the display, so any screen meant for an RPi works with it.

👀 Now I see that the standoffs on the display match up with mounting holes in the panel.  It's a bit odd that the display will sit naked on top rather than inside a bezel, but I suppose the raw look isn't so bad.

> There's the BTT TFT50... Then there's the BTT PI TFT50

🎉 Aha!  Okay, that clears it up -- I did a smidge of Googling before I opened this issue, trying to see if there was something different, but I only saw the Pi-only version in results (I didn't try very hard, tbh).

Groovy, thanks!

I may try to make some time to design a panel that is specific to the BTT PI TFT43/TFT50 that lets the display sit flush behind the panel, if that would be welcome.  The [Raspberry Pi TFT](/jon-harper/OmniBox/tree/main/Panels/Display/Raspberry%20Pi%20TFT) panel is fine, but since this project is about options...

jon-harper, 2023-01-12:
> It's a bit odd that the display will sit naked on top rather than inside a bezel, but I suppose the raw look isn't so bad.

Apologies for that; I don't own an RPI screen, so I took the lid mount and spliced it on a display panel--the only thing I could be sure wouldn't have clearance issues.

> Groovy, thanks!

Glad to help! Thanks for pointing out the doc issues. I knew that area needed work, but hadn't looked at it in awhile. Out of sight, out of mind...

> I may try to make some time to design a panel that is specific to the BTT PI TFT43/TFT50 that lets the display sit flush behind the panel, if that would be welcome. The [Raspberry Pi TFT](https://github.com/jon-harper/OmniBox/tree/main/Panels/Display/Raspberry%20Pi%20TFT) panel is fine, but since this project is about options...

🤝🤝🤝 Flush mount designs are definitely welcome! I love a universal mount, but I love a nice fit better (and plenty of options, too).

MaffooClock, 2023-01-13:
I've got a rough design, but I think it's pretty dang close.  The only concern I have is the depth, namely whether the rear shell will intrude on the lower bay trays area.

I'll print and test the fit, make whatever tweaks may be necessary, then hopefully be close to opening a PR...

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

jon-harper, 2023-01-13:
Flush mount? Nice!

On Fri, Jan 13, 2023, 12:27 PM Matthew Clark ***@***.***>
wrote:

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

MaffooClock, 2023-01-14:
Success!  First print, everything went together smoothly, and I had no clearance issues behind it.  The mounting ears on the rear shell require supports, so I made them kinda beefy and kept them flat to make removing supports easy and reduce risk of breaking.

BOM:

1. 8 x M2.5x6 BHCS or FHCS for attaching display to rear shell (could get away with just 4)
2. 4 x M3x5ODx4L heat-set inserts (for HSI version)
3. 4 x M3x6 BHCS or FHCS for attaching rear shell assembly to front panel

This is just for the Pi TFT50; no plans at the moment to do the Pi TFT43, maybe we'll see if anyone asks for it.

If you dig it, I'll open a PR for you to review.

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

jon-harper, 2023-01-14:
I am all about this. Whenever you feel it's ready, open that pull request!

Side note: formal support for M3x5x4mm inserts is coming.

jon-harper, 2023-01-27:
Reopened this so I don't forget to add to the docs.

MaffooClock, 2023-01-27:
I thought I'd take a crack at the documentation, too.  See commit [6b9dca5](https://github.com/MaffooClock/OmniBox/commit/6b9dca5ca3b3cddd1df16bf05d8939f4c6262524) to review.

Aside from just adding the relevant section, I also added a note to the "Raspberry Pi Displays" section.  Not sure how you'd feel about that -- maybe you don't want the note, or maybe you might remove this display from that section altogether.

If you're okay with going this route, then add comments to that commit of any changes you'd like to see, then I'll open a PR afterward.  Or I could open a PR as-is, if it's mostly right, and I guess you can make edits before accepting the PR (I'm not a GitHub expert)?  Or heck -- copy/paste what I've done as a starting point if that'd be easier on you (I don't care about credit, just want to help).  Or purple, because ice cream has no bones!

jon-harper, 2023-01-27:
I think I can cherry-pick across forks, so I will try that. Regardless of how I add it, your work is definitely helpful and very much appreciated.

jon-harper, 2023-02-16:
Okay, it's documented. I completely reworked that section of the docs, too. It should be a lot clearer now.

Closed 2023-02-16.

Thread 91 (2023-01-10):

Display template is faulty

jon-harper, 2023-01-10:
A user reported that the display template has the wrong mounting hole locations. The template is inherited from Steve's project, so it very well may never have been updated.

MaffooClock, 2023-01-17:
I used this template for my BTT Pi TFT50 display (#88), and while those components fit together perfectly, I did notice the mounting holes in the corners were slightly off from those in the main body; ~1-2mm vertically inward (horizontal spacing lines up fine).

I started to bring this up, but figured it might be possible that my main body component warped slightly during printing, so I didn't want to say anything until I was certain.  I wanted to check the design file for the main body to see what the vertical distance is between mounting holes to compare with those in the template (and my designed based off that), but I don't see a .f3d or .step file.

I'll hold off on submitting a PR #88 until we can confirm correct spacing.

jon-harper, 2023-01-17:
Thank you for checking on this; there are a couple of entangled display bugs/requests here I need to sort out. I intend to pare down the bug list later this week, hopefully knock this one out, and get some new stuff merged. :smile:

MaffooClock, 2023-01-23:
Now that you got this sorted out, what is the vertical distance between screw holes supposed to be?  As a test, I re-printed my BTT Pi TFT50 with 103mm vertical distance, and it was spot-on (horizontal distance was unchanged).

I'll submit a PR for the new display panel once I know the correct measurement 👍

jon-harper, 2023-01-23:
103.825mm 😊

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

Closed 2023-01-22.

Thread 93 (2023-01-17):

Add HSI to crossbar

jon-harper, 2023-01-17:
An option to print the crossbar with inserts would let the user tighten the screws down until the bar does not turn.

Closed 2023-03-16.

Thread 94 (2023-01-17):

Add a power switch cover to prevent accidental bumping

jon-harper, 2023-01-17:
The power switch is too easily bumped and can power down the printer on accident.

Solutions:

1. Add a switch cover plate
2. Implement the suggestion of a hard-throw switch that won't flip so easily.

MaffooClock, 2023-01-17:
Funny... I was just thinking about this the other day.

My thought would be to add guard rails on either side.  It could be an add-on piece, so the base would have an alternate design that would allow this extra piece to be affixed over the switch.

Something similar to this (doesn't need to look like this, I just found it in a Google Images search as an example):
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

This design makes it easy to turn on, difficult to turn off (accidentally).

jon-harper, 2023-02-09:
Hey Matthew. [This commit}(https://github.com/jon-harper/OmniBox/commit/72bce84f87fa234fad469b4650a23c19bb79bdec) seems to do the job if you want to give it a shot.

The power switch needs about 1mm clipped from the ends of the snap-in "ears" to make room for the cover.

MaffooClock, 2023-02-09:
Well done 👍  I will definitely print one and check it out!

jon-harper, 2023-02-16:
Switch cover is now [merged in main](https://github.com/jon-harper/OmniBox/commit/48f5374f79bf7ff902ebda646f5c765db5af0da4). I'll close this after the docs are done.

jon-harper, 2023-05-17:
I've added the switch to all of the 0.9.10 docs but the assembly portion.

Closed 2023-05-17.

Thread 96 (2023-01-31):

Would love to see a tray for a 5V PSU

piotrb, 2023-01-31:
I have a Mean Well RS-25-5 PSU kicking around this thing is quite small, it could easily fit on a tray ..

This could be a nice semi standard config for running the CPU on a separate power supply (so you can turn off the big power supply when not needed)

Here is the datasheet with dimensions: https://www.meanwellusa.com/upload/pdf/RS-25/RS-25-spec.pdf

Thoughts?

jon-harper, 2023-01-31:
There is a user who was working on this last week and discussed it in Discord. I've sent them a ping. I do think this is a nice add, but one I haven't been able to do without buying one.

jon-harper, 2023-01-31:
Here's what they are working on (user edgy on the OmniBox Discord):

> oh, yeah.  i haven't printed my design yet but based on the datasheet and dummy model in freecad it should work.  the rs-25-5 is wider than one of the short trays so i extended it a little with the intention of placing it in the center of the lower bay using the extra space towards the back (probably fit in the rear bay also, but i'm planning to place a long tray with wagos there).  the fan mount was made super simple (and probably not thick enough for the screws) so it could be skipped if not needed.
> the rs-25-5 could easily fit on a long tray and i haven't sketched that out yet since it didn't fit my initial use case but wouldn't take long to do.

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

In short, it's in progress. :-)

jon-harper, 2023-02-27:
edgy published his mod [here on Printables](https://www.printables.com/model/388529-omnibox-lower-bay-trays-for-mean-well-rs-25-5).

I'll close this once I've got the docs caught up.

Closed 2023-03-23.

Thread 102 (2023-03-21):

Templates should have a version code

jon-harper, 2023-03-21:
Templates for trays and panels should have a printed (concealed) tag for the template version.

Most panels and trays still use version 1, but CPU trays and MCUs are on V2. It'll be better to fix this before more time passes.

jon-harper, 2023-07-23:
Finished parts are merged into `0.9.10-beta` for release.

Closed 2023-07-23.

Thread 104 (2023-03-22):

Dedicated Base for 500w Power Supply

jon-harper, 2023-03-22:
### Discussed in https://github.com/jon-harper/OmniBox/discussions/100

<div type='discussions-op-text'>

<sup>Originally posted by **DannyKlenz** March 14, 2023</sup>
Would you be willing to give the 500w power supply its own part that doesn't require the extensions?</div>

jon-harper, 2023-03-23:
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

Highlighted is the standard base. This is one piece that is 10mm taller (the height of the shim). It is HSI only at the moment.

I've also updated the other unified bases to the 0.9.10 testing versions.

[Available in `unstable`](https://github.com/jon-harper/OmniBox/tree/unstable/Core/Base/Unified)

jon-harper, 2023-07-23:
This is merged in and documented.

Closed 2023-07-23.

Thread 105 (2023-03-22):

[REQUEST] BIGTREETECH TFT35 SPI V2.1 Touch Screen Display Mount

YFNOtaku, 2023-03-22:
https://biqu.equipment/collections/lcd/products/bigtreetech-tft35-spi-v2-1-touchscreen-io2can-module

I have one of these in the mail now to add to my system, and was hoping someone with more modeling skill than I (which is none currently) could help me with this. Don't really care if it's a front or top mount, I would appreciate either. Also found a case that you could use as a potential starting point. Thanks in advance!

https://www.printables.com/model/403192

jon-harper, 2023-10-13:
I was going through old issues and realized I never replied to this. I was holding off replying until I could find out if anyone has one of these to model against, and then forgot. I am so sorry!

Display mounts are a little more involved to design than, say, an MCU tray, where you have just four holes and no real clearance issues. I don't have this display to work against, but I can try via CAD alone if you're still in need of a display mount and can test.

jon-harper, 2024-11-28:
I'm going to close this as wontfix. I'm open to contributions, however.

Closed 2024-11-28.

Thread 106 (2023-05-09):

Display template needs to be updated

jon-harper, 2023-05-09:
This issue is related to #102, as the new template will have a version code, as well.

Flow4enol and I spent some time fussing with the display template, which is the sole remaining legacy part from Steve Burcham's original cases. He was kind enough to create a new template, but it's not integrated into the Fusion files yet.

jon-harper, 2023-07-30:
Now updated to version 3.

Closed 2023-07-30.

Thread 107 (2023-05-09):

Fit Test: New LRS-350 PSU tray

jon-harper, 2023-05-09:
This tray is adjusted from the stock version to make room for M4 socket head cap screws.

[Files are in `unstable`](https://github.com/jon-harper/OmniBox/tree/unstable/Trays/PSU/Mean%20Well%20LRS-350)

jon-harper, 2023-06-28:
Tested by Flow4Enol

Closed 2023-06-28.

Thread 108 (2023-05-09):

Fit Test: New RSP-500 PSU tray

jon-harper, 2023-05-09:
This version is modified to make room for M4 socket head cap screws.

[Files are in the `unstable` branch.](https://github.com/jon-harper/OmniBox/tree/unstable/Trays/PSU/Mean%20Well%20RSP-500)

cereal7802, 2023-05-13:
I don't have M4 socket caps to test with right now (they are coming), but the tray works fine. The only issue I had was that with fans(4010) mounted in the PSU tray area, the psu does not fit as it is longer than the LRS-350. It does fit fine with no fans mounted and probably doesn't need them as the rsp-500 has a fan built in it that moves a decent amount of air.

jon-harper, 2023-05-13:
Thanks for checking! I'm going to hold this open until I can verify the socket head screws fit, just to be sure.

Re: the tray fit

The RSP-500 pretty much maxes out the space below. Since the fan up front blows out, I moved it forward to let the existing fan try and do the work (and try and leave more room at the back).

There's a work in progress to center the PSU fan exhaust on the fan holes, but that's still in planning.

jon-harper, 2023-07-20:
I'm going to close this for now. CAD shows there's plenty of room for socket head screws and cereal's already made sure it fits.

Closed 2023-07-20.

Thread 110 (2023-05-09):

Dual Tray: Pi Mounts + Creality Mounts

jon-harper, 2023-05-09:
This will fit a Creality-style board and a Pi-style board (e.g. BTT SKR Pico).

jon-harper, 2023-06-19:
This just needs documentation. Will fix when I figure out how to do dual tray combos in the docs. LOL.

Closed 2023-07-26.

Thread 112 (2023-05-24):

50mm fan cage is too short

jon-harper, 2023-05-24:
This is probably a pretty simple error, but I don't have time to fix ATM and do not want to forget again.

jon-harper, 2023-06-05:
Fixed in the beta branch.

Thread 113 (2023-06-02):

Large PSUs do not work with toggle switches

jon-harper, 2023-06-02:
The RSP-500 and LRS-*450* (not 350) are too large for toggle switches. Rocker switches (or an alternate location) are needed for these PSUs.

jon-harper, 2023-06-10:
This is now documented.

Closed 2023-06-10.

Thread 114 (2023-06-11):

Lower bay tray standoffs should be tapered

jon-harper, 2023-06-11:
The lower bay tray standoffs have a 3mm fillet. A tapered edge (draft/chamfer) would prevent standoffs from breaking as easily.

jon-harper, 2023-07-09:
Implemented with the fix for #120 .

Closed 2023-07-09.

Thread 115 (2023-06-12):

BTT 3.5" TFT E3 V3.0 does not fit the stock 12864 mount

jon-harper, 2023-06-12:
I'm a little shocked about this, since the part should be a drop-in replacement. The CAD shows the same issue.

Reported via Discord.

jon-harper, 2023-06-16:
https://github.com/jon-harper/OmniBox/tree/unstable/Panels/Display/BTT%203.5%20TFT%20E3

Fix for fit testing.

jon-harper, 2023-06-18:
Mounts needs to expand by up to 1mm around the display to account for hand-soldering sloppiness.

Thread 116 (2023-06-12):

Mean Well LRS-600 Support

jon-harper, 2023-06-12:
Requested by Theo Bromine via Discord.

Notes:
- 40mm fans will not fit in the front panel.
- Recommend an open bottom panel for airflow.
- Requires a taller base like the RSP-500 (see third picture)

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

jon-harper, 2023-06-12:
Files for fit testing: https://github.com/jon-harper/OmniBox/tree/unstable/Trays/PSU/Mean%20Well%20LRS-600

jon-harper, 2023-08-19:
Tested and in `main`

Closed 2023-08-19.

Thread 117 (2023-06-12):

IEC socket can be inverted in the base

jon-harper, 2023-06-12:
Flipping the IEC socket would move the connectors away from the PSU and leave more room in the PSU bay.

jon-harper, 2023-10-13:
This is included in 0.9.11 now.

Closed 2023-10-13.

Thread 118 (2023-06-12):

Move PSU tray mounts forward

jon-harper, 2023-06-12:
I'm going to use this terrible illustration:

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

The base can be modified to mount the PSU with 4 screws and provide a better join between the front and rear base.

1. Move the PSU tray mount forward about 20mm. (red/white)
2. Cut out that area in the front base. (red)
3. Modify the rear base so that instead of an interior cutout, it has an exterior cutout. Basically, move the walls inwards. (blue)
4. Extend the front base to cover the rear base. This covers the joint between the two bases. (tan)
5. Continue using 8 screws to mount as normal (yellow)

Targeting 0.9.11 for this modification.

jon-harper, 2023-10-16:
Ready for the beta.

Closed 2023-10-16.

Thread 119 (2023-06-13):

Mean Well SE-450 Support

jon-harper, 2023-06-13:
This requires a 10mm base extension (shim, Extended Unified Base, or other method of lifting the base 10mm).

*Rocker switch support only.*

[Files](https://github.com/jon-harper/OmniBox/tree/unstable/Trays/PSU/Mean%20Well%20SE-450)

I will perform the fit test for this shortly, as I have a spare SE-450 and intend to use it. :wink:

jon-harper, 2023-06-28:
This is done. Fits nicely.

Closed 2023-06-28.

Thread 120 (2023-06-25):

0.9.10-beta HSI profile causes inserts to bulge at the edges

jon-harper, 2023-06-25:
I've done some testing. Top left is current insert profile, 4.7mm with no hole taper.

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

I'm currently implementing the change to a 5.0mm diameter hole with a 4 degree inward taper at the base.

The result will go in `unstable` until a user has printed and tested. From there it will go into the beta branch.

jon-harper, 2023-07-09:
This fix is included in 0.9.10-beta now.

Closed 2023-07-09.

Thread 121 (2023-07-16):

Heat set insert practice block needs updating

jon-harper, 2023-07-16:
See issue #120 changes.

The practice block has the old insert profiles and needs to be updated.

Closed 2023-07-18.

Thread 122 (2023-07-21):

Fit test for 50mm x 10mm and 50mm x 15mm axial fans

jon-harper, 2023-07-21:
50x12 fans are tested, but 50x10 and 50x15 fans are not. Note that these are not 5015 blowers.

jon-harper, 2023-09-28:
I'm having trouble finding 50mm x 10mm fans that are not actually 12mm deep.

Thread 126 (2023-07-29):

Storage CPU Trays

jon-harper, 2023-07-29:
This is a placeholder issue for the implementation of the storage CPU tray.

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

https://github.com/jon-harper/OmniBox/tree/0.9.10-beta/Trays/CPU/Storage%20Tray

Closed 2023-07-29.

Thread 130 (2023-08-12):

Additional IEC socket and switches for the base

jon-harper, 2023-08-12:
1. IEC sockets with an integrated switch can be made to fit taller bases.
2. A front base without a power switch would then be useful.

jon-harper, 2023-10-16:
The integrated switch will have to be added to a rear panel; the base would be far too tall if I do this.

I have added bases without power switches or IEC sockets.

Closed 2023-10-16.

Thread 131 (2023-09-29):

Print Guide: add note about tuning and belt tension

jon-harper, 2023-09-29:
CoreXY printers are susceptible to printing askew if belt tension is unequal. Additionally, belt tension is key to getting a dimensionally-accurate print. The print guide should have information on what to check for in tuning, perhaps links to external resources, as well.

jon-harper, 2024-03-05:
Added

Closed 2024-03-05.

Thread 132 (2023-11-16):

Assembly Guide: wire routing and planning for maintenance

jon-harper, 2023-11-16:
Leaving a little slack on the wires is the difference between a nightmare and a serviceable case. Make a note of this.

jon-harper, 2023-11-16:
Also, add connectors to panel fans. This allows removing the panel and disconnecting the fan, as well.

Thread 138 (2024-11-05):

[Request] Inovato Quadra T95 Mini CPU

theweeirish, 2024-11-05:
Im looking if it is possible for a tray for the Inovato Quadra t95 mini board to be mounted inside.

https://www.alibaba.com/product-detail/New-Upgrade-T95-Mini-Android-9_1600134469365.html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

Its an alt for using a pi, I can also modify an existing tray if provided.

Thanks.

jon-harper, 2024-11-28:
I apologize for the delay in replying here. That will fit on a long lower bay tray (or two). Look at the lower bay tray template as your most likely option here. I won't be able to make this myself, so I'm closing this issue.

If you have any other questions, drop on by Discord for a faster response. :-)

Closed 2024-11-28.

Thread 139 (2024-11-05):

[Request] Nitehawk 36 USB Board Tray

theweeirish, 2024-11-05:
Im looking for a tray for the nitehawk 36 usb board.

https://docs.ldomotors.com/en/Toolboard/nitehawk-36

Let me know if you need anything.

jon-harper, 2024-11-28:
This could be done one of a couple ways. Maybe a lower bay tray, or a mount on the rear or a side panel?

Do you have a STEP file or can you point me to one?

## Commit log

2022-05-11 Readme and main body fixes
    [Main Body - Front.stl]
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2022-05-11 Fix for CPU tray fit
    [Main Body - Front.stl]
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2022-05-12 Front panel fixes
    The blank and vent versions are not updated yet, but the panel is now thicker.
    [MicroSD Extension - Front Panel.stl, MicroSD Extension - Outer Shell.stl]
2022-05-14 New tray; main body fixes
    [Lower Bay Tray - LM2596 with LED.stl, Main Body - Front.stl]
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2022-05-16 Fixed carry lid
    Added more screw holes anchor and ridging to prevent bowing.
    [Carry Lid.stl]
2022-05-18 Front panel fixes and updates
    [Front Panel - Blank.f3d, Front Panel - Blank.step, Front Panel - LANMU SD Card Cutout.stl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]
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2022-07-02 Fixed issue #1
    Fixed #1 , screw holes are uniform now.
    [Base - Front.stl, Base - Rear.stl, Carry Lid.f3d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]
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2022-07-03 Display panel templates and fixes
    [BTT TFT 3.5 Display Mount.stl, BTT TFT 3.5 Display Panel.stl, Display Mount.f3d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]
2022-07-03 SKR E3 and Creality 1.1.,X support
    As requested by poddy71 on reddit.
    [MCU Tray - BTT SKR E3.f3d, MCU Tray - BTT SKR E3.step, MCU Tray - BTT SKR E3.stl]
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2022-07-04 Fixed SKR E3 tray, added MCU folders
    [MCU Tray - BTT SKR 2.f3d, MCU Tray - BTT SKR 2.step, MCU Tray - BTT SKR 2.stl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]
2022-07-07 Tray fixes
    [CPU Tray - RPi 4B.f3d, CPU Tray - RPi 4B.step, CPU Tray - RPi 4B.stl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]
2022-07-07 Fixed SKR series mount profile
    Fixed #2 and renamed files from SKR 2 to SKR
    [MCU Tray - BTT SKR 2.f3d, MCU Tray - BTT SKR 2.step, MCU Tray - BTT SKR.f3d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]
2022-07-07 Fixed LM25496 w/LED tray; added subfolders
    May need to add a second set of tray profiles as there are two very similar LM2596s with LEDs available.
    [Lower Bay Tray - 40mm Fan and Two Bucks .f3d, Lower Bay Tray - 40mm Fan and Two Bucks v2.stl, Lower Bay Tray - 40mm Fan and Two Bucks.step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]
2022-07-08 Renamed SKR E3 files
    Since the E3 Turbo is supported, I took the "Mini" out of the name.
    [MCU Tray - BTT SKR E3.f3d, MCU Tray - BTT SKR E3.step, MCU Tray - BTT SKR E3.stl]
2022-07-13 New rear body without fans cutouts
    New rear panels with fan cutouts coming soon.
    [Base - Rear No Fans.stl]
2022-07-19 New rear base and rear panels
    - Moved all old rear panels to an outdated folder.
    - Added templates for lots of different types of generic panels.
    - New rear base with integrated IEC socket.
    - 60mm fan cage for the new rear panels.
    [60mm Fan Cage.stl, 60mm Fan Gasket, TPU.stl, Base - Rear.stl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]
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2022-07-20 Fixed depth of 60mm fan cage
    [60mm Fan Cage.stl]
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2022-07-20 Fixed #5 - Display mount profiles
    Fixed #5
    [Main Body - Front.stl]
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2022-07-20 Awful name mixup fixed
    [Main Body - Rear No Fans.stl]
2022-07-20 Re-export
    - Fixed overhang needing supports on front main body.
    - Re-exported rear body for final test print before release.
    [Main Body - Front.stl, Main Body - Rear No Fans.stl, Main Body - Rear.stl]
2022-07-21 Fan cages for both 6015 and 6020 fans
    [6015 Fan Cage.stl, 6015 Fan Gasket, TPU.stl, 6020 Fan Cage.stl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]
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2022-07-23 Fan Cages have a folder now
    There are now enough fan cage files to create a folder for them.
    [4010 Fan Cage.stl, 4010 Fan Gasket, TPU.stl, 4020 Fan Cage.stl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]
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2022-07-23 Added version of main body with fan intake
    [Main Body - Front with 60mm Fan.stl]
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2022-07-24 Final fixes for 0.9.7
    [Main Body - Front with 60mm Fan.stl]
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2022-07-24 Fixed #5
    Fixed #5 - screen mounting holes
    [Main Body - Front with 60mm Fan.stl, Main Body - Front.stl]
2022-07-26 More logical names for Core parts
    Main body is now three components:
    1. Front
    2. Rear
    3. Crossbar
    Front and rear may have variants.
    [Main Body - Crossbar.stl, Main Body - Front No Fans.stl, Main Body - Front with 60mm Fan.stl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]
2022-07-26 RPi TFT Display mount for #3
    #3 - Added display mount for a Raspberry Pi TFT (instead of a lid).
    [Display Mount - Raspberry Pi TFT.f3d, Display Mount - Raspberry Pi TFT.step, Display Mount - Raspberry Pi TFT.stl]
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2022-07-27 Fixed #11 and added PSU type folders to Core
    - Fixed #11
    - Core now has two subfolders for PSU type
    If anyone has ideas for a universal PSU mount, I'm all ears.
    [Main Body - Front No Fans.stl, Main Body - Front with 60mm Intake.stl, Main Body - Rear No Fans.stl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]
2022-07-27 Revert "Fixed #5"
    This reverts commit c031e1b363254276bf5413c7c5fb7f4a952b5a2c.
    [Main Body - Front with 60mm Fan.stl, Main Body - Front.stl]
2022-07-27 Ensuring an old fix was not lost
    The screen hole mount fix was pushed into main, but I may have accidentally not pulled it into 0.9.8. I've re-exported the STLs and will commit them into main, as well.
    [Main Body - Front No Fans.stl, Main Body - Front with 60mm Intake.stl]
2022-07-27 PSU screw size correction
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2022-07-28 Organized and updated buck trays
    Both the DROK and compact HiLetGo buck converters now have identical single (small) and dual (normal-sized) trays made from a template.
    [DROK LED Bucks.f3d, DROK LED Bucks.step, HiLetGo LED Bucks.f3d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]
2022-07-28 Template updates;' moved all templates to folders
    - New lower bay template file
    - New MCU tray template file
    - All template files are now in subfolders
    [Front Panel - Micro SD Extension with USB C.step, Front Panel - Micro SD Extension with USB C.stl, Front Panel - Template.f3d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]
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2022-07-29 Documentation edits, fixes, and formatting
    - Clarified numerous examples and explanations
    - Broke out certain parts of the BOM and printing guide to clarify details
    - Corrected some fastener mistakes in the BOM and assembly
    - Updated printing guide with new info
2022-07-29 Creality MOSFET variations, lower bay templates
    Creality MOSFET tray now comes in a small and large version.
    Lower bay template is updated with some parametric values for screw holes.
    Also added a Parametric Mount Generator for simple, 4-hole mounts like buck converters.
    [Lower Bay Tray - Creality MOSFET - Large.stl, Lower Bay Tray - Creality MOSFET - Short.stl, Lower Bay Tray - Creality MOSFET.f3d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]
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2022-08-01 Updated gallery and BOM for 0.9.8
    Also cleaned up the wording a bit around assembling panels and fixed some links.
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2022-08-02 Fan cage fixes and doc edits
    [8020 Fan Cage.stl, 8020 Fan Gasket.stl, 8025 Fan Cage.stl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]
2022-08-02 Airflow improvements
    - Increased side teeth size from 4mm to 6mm
    - Air intakes in front of base
    - Optional 40mm fan mount in front, as well
    [Base - Front.stl, Base - Rear.stl]
2022-08-03 Updated all buck trays and templates
    - All bucks now have dual and single mounts
    - Full trays now come with a fan option
    [DROK LED Bucks.f3d, DROK LED Bucks.step, DROK LM2596 with LED.f3d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]
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2022-08-04 Added work-in-progress guided tour
    This will replace part of the printing guide
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2022-08-05 FIxed #16
    This adds a version stability guarantee notice to the main landing page.
    Between the earlier release log commit and this one, this fixes #16 .
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2022-08-07 Fixed #17
    - Screw holes needed more room than on the XY axis due to layer unevenness.
    - Screw holes are 6.4mm, which seems to fit nicely.
    - Updated all variants
    [Main Body - Front No Fans.stl, Main Body - Front with 40mm Intake.stl, Main Body - Front with 60mm Intake.stl]
2022-08-08 Added 7mm base extensions for tall PSUs
    This relates to issue #11 and RSP-500 support.
    The SE-450 will need 10mm extensions, so multiple heights will probably be added in the future.
    [Base - Front Extension.stl, Base - Rear Extension.stl]
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2022-08-14 Missed a fan
    [6025 Fan Cage.stl, 6025 Fan Gasket, TPU.stl]
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2022-08-15 Prepping front panel folder for 0.9.8
    - Added readme.md
    - Removed old files
    - Renamed LANMU MicroSD holder
    - Added new master template file
    [Front Panel - Keyhole Vents.stl, Front Panel - Master.f3d, Front Panel - Micro SD Extension with USB C.step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]
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2022-08-17 Testing new tray for issue #19
    - This needs testing, but is designed for a Fotek SSR-40 DA solid state relay.
    - Not certain if the side supports for the SSR are adequate.
    [Lower Bay - SSR-40 DA.stl]
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2022-08-17 Fix for #20
    Added half dual tray and updated parametrics, readme
    [Lower Bay Tray - Generic LM2596 - Half Dual Tray.stl, Lower Bay Tray - Generic LM2596.f3d, Lower Bay Tray - Generic LM2596.step]
2022-08-18 Fixed some file names
    [Lower Bay Tray - Generic LM2596 - Full Dual Tray.stl, Lower Bay Tray - Generic LM2596 - Full Dual with Fan.stl, Lower Bay Tray - Generic LM2596 - Full Single w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]
2022-08-18 Missed some rear main bodies; re-exporting all of them
    [Main Body - Front with 40mm Intake.stl, Main Body - Front with 60mm Intake.stl, Main Body - Rear No Fans.stl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]
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2022-08-19 FIxing USB A/B confusion
    [Ender 5 Plus - USB B.stl, Rear Panel - Generic Panel USB B.step, Rear Panel - Generic Panel USB B.stl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]
2022-08-19 FIxing USB A/B mixup
    [Front Panel - MicroSD, USB B, Hexagons.stl, Front Panel - MicroSD, USB B, Slats.stl, Front Panel - MicroSD, USB B, Slots.stl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]
2022-08-20 New lid with filament roller
    This is based on my Tighter TUSH project on Thingiverse.
    [Lid - Spool Roller.f3d, Lid - Spool Roller.step, Lid - Spool Roller.stl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]
2022-08-20 Drybox holder lid for Rubbermaid containers
    There may be two more of these coming in different formats.
    [Lid - Drybox Holder - Rubbermaid 21qt.f3d, Lid - Drybox Holder - Rubbermaid 21qt.step, Lid - Drybox Holder - Rubbermaid 21qt.stl]
2022-08-21 Correct source file error
    [Lid - Drybox Holder - Rubbermaid 21qt.f3d]
2022-08-24 Display folder cleanup; chamfers not fillets
    - Consistent file names across all display mounts
    - All display panels are switched to chamfers on the build plate edges instead of fillets. This should provide a better surface and maintain consistency with the rest of OmniBox.
    [BTT TFT 3.5 Display Mount.stl, BTT TFT 3.5 Display Panel.stl, Display Mount - BTT TFT24.f3d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]
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2022-09-05 Working stackable lid
    This needs refinement for a better "set" between the lid and case it stacks with, but it definitely works.
    [Lid - Stackable Case.stl]
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2022-09-06 Reduced print time, material usage
    Lengthened the support ridges that run front to back.
    [Base - Front.stl, Base - Rear.stl]
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2022-11-01 Fixed LM2596 mounting holes
    Fixed #51
    [Lower Bay Tray - Generic LM2596 - Full Dual Tray.stl, Lower Bay Tray - Generic LM2596 - Full Dual with Fan.stl, Lower Bay Tray - Generic LM2596 - Full Single w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]
2022-11-26 Merging in 0.9.9 (#72)
    Squashed all commits as the file hierarchy is different.
    [12025 Fan.f3d, 12025 Fan.step, 4010 Fan Cage.stl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]
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2023-01-21 Updated MKS Skipr
    Added both a stock and an HSI version. The original Killajoedotcom contrib uses 4mm inserts; this one uses 5.7mm to match the rest of the case.
    [MCU Tray - MKS Skipr - 5mm HSI.3mf, MCU Tray - MKS Skipr - HSI.stl, MCU Tray - MKS Skipr - Stock.stl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]
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2023-01-21 added STLs for Rasbperry Pi Touch Display (#89)
    Panel design by Anton Chebotaev <anton@chebotaev.net>
    [screen_case_flat.stl, screen_case_raised.stl, screen_plate_raised.stl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]
2023-01-22 Fixed #91
    Screw holes were definitely off, probably from v0.9.5 -> 0.9.7.
    [Display Mount - Template M4.f3d, Display Mount - Template M4.step, Display Mount - Template.f3d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]
2023-01-22 Fixing display panel bugs
    [Display Mount - BTT TFT24.f3d, Display Mount - Mini 12864 - Panel.stl, Display Mount - Raspberry Pi TFT.f3d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]
2023-01-22 Fixing the fixes
    [Display Mount - Template M4.f3d, Display Mount - Template M4.step, Display Mount - Template.f3d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]
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2023-01-27 Adding display panel for BTT PI TFT50 (#95)
    [Display - BTT PI TFT50.f3d, Display - BTT PI TFT50.step, Display Mount - BTT PI TFT50.stl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]
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2023-05-08 Reverted built-in supports
    [Main Body - Front - HSI.stl, Main Body - Front - Stock.stl, Main Body - Rear - Stock - Dual 40mm Fans.stl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]
2023-05-08 Added power switch label to stock front base
    [Base - Front - Rocker Switch.stl]
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2023-05-08 Updated missed files
    [Main Body - Rear - HSI - Dual 40mm Fans.stl, Main Body - Rear - HSI - No Fans.stl]
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2023-05-09 Fixed panel thickness
    [Side Panel - Internal 40mm Fan - Hexagons.stl, Side Panel - Internal 40mm Fan - OmniBox Logo.stl]
2023-05-09 Fixed the fix
    [Side Panel - Internal 40mm Fan - OmniBox Logo.stl]
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2023-05-24 Fixed a screw hole
    [Side Panel - Internal 40mm Fan - Hexagons.stl]
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2023-06-05 Added some missing STEPs
    [4010 Fan Assembly.step, 6015 Fan Assembly.step, 8025 Fan Assembly.step]
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2023-06-17 Fixed file names
    [5012 Fan Cage.stl, 5012 TPU Gasket.stl]
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2023-07-09 Part fix for #120
    [Main Body - Crossbar - HSI.stl, Main Body - Front - Full HSI.stl, Main Body - Rear - Full HSI.stl]
2023-07-09 More fixes for #120
    [Base - Front - Full HSI.stl, Base - Rear - Full HSI.stl, Base - Unified Extended - HSI.stl]
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2023-07-13 Merging in from unstable
    [Side Panel - 50mm Fan.f3d, Side Panel - 50mm Fan.step, Side Panel - External 50mm Fan.stl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]
2023-07-18 Update hole dimensions
    Fixed #121
    [Heat Set Insert Practice Block.stl]
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2023-07-23 Added version code to templates
    Fix for #102
    [Bottom Panels - Template v2.step, Display Mount - Template.f3d, Display Mount - Template.step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]
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2023-07-28 Tightened MF3 clip dimensions
    [Panel Mount Profiles.f3d, Panel Mount Profiles.step]
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2023-07-31 Fixing lost files
    [Base - Front - Full HSI.stl, Base - Front - Rocker Switch.stl, Base - Front - Stock - Rocker Switch.stl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]
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2023-10-07 File name fix
    [Bottom Panel V3 - Mean Well Unified.stl]
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2023-11-11 Dual 60mm rear panel; replaces E5+ panel
    [Rear Panel - Dual 60mm - HSI USB A.stl, Rear Panel - Dual 60mm - HSI USB B.stl, Rear Panel - Dual 60mm - HSI USB C.stl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]
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2023-11-14 Fixed text
    [PSU Mount - RSP-500 - Left HSI.stl, PSU Mount - RSP-500 - Left.stl]
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2024-02-26 Fixed IEC HSI holes
    [Base - 36mm Rear - IEC HSI.stl, Base - 42mm Rear - IEC HSI.stl]
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2024-02-28 Fixed lower bay screw holes
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2024-03-07 Reverting; renaming
    [Lower Bay Tray - Parametric Mount Generator.f3d, Lower Bay Tray - Template.f3d, Lower Bay Tray - Template.step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]
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2024-03-09 Importing unstable parts
    [5010 Fan.step, 5015 Fan.step, BTT SKRat.step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]
2024-03-15 Revert "Importing unstable parts"
    This reverts commit bd6d7db31c7669fa0067aa4596377a283272c79b.
    [5010 Fan.step, 5015 Fan.step, BTT SKRat.step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]
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2024-07-03 Tweaked tightness
    [Keystone Jack.step, Side Panel - Keystone - 3 Keys.step, Side Panel - Keystone - 3 Keys.stl]
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
